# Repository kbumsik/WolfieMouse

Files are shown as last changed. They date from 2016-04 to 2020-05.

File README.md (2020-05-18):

# WolfieMouse

WolfieMouse is a robotics project to build [a micromouse](https://en.wikipedia.org/wiki/Micromouse). This project covers three parts:

* Robotics algorithm for maze solving (C++)
* low-level hardware driver software (C and ARM assembly)
* Tools to capture and plot robot's sensor data (Python)
* Embedded hardware design and PCB design (KiCad, an open-source alternative to Altium)

This robot won:
  * **The Special Mention Award in 2018 IEEE Region 1 Micromouse Robotics Competition**.
  * **The 3rd Place Award in 2019 IEEE Region 1 Micromouse Robotics Competition**.

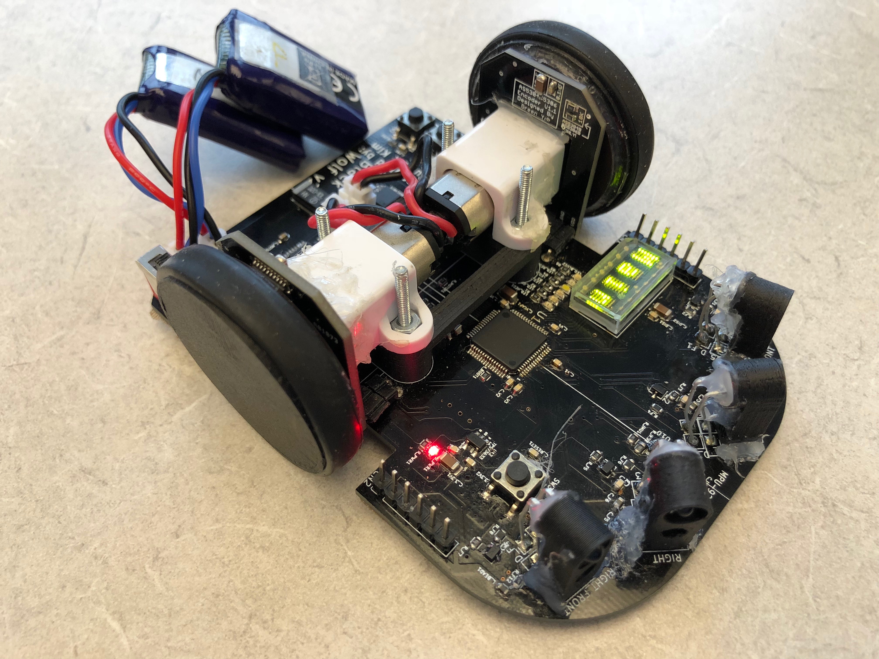
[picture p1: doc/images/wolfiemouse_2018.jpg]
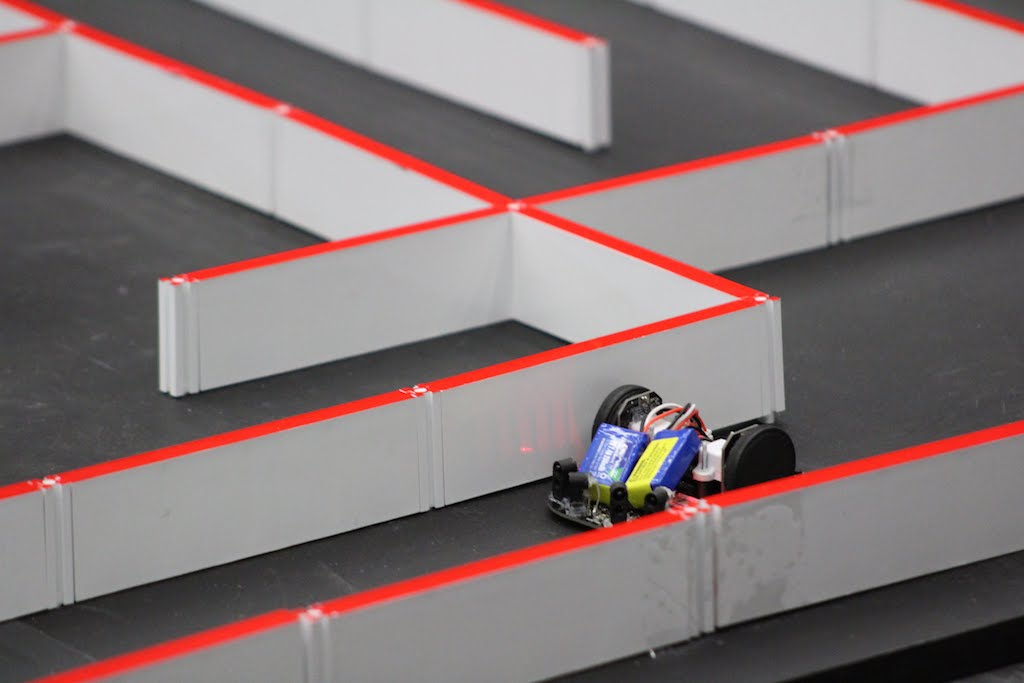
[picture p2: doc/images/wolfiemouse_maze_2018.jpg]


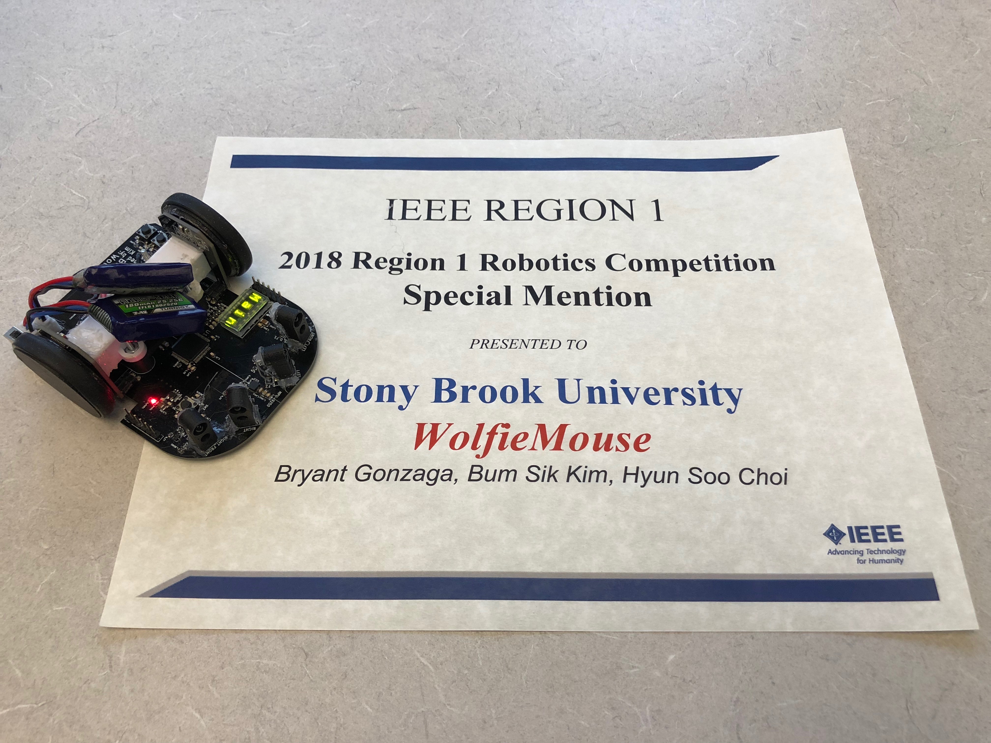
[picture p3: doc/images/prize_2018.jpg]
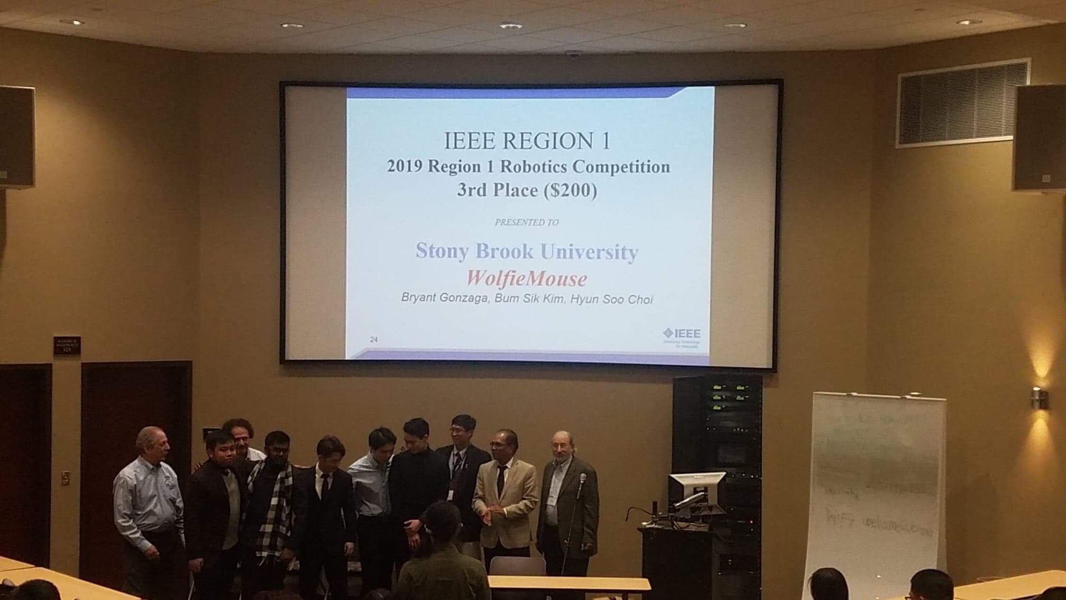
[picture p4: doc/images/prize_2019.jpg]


## Get started

If you don't know what is micromouse competition, [this document will help.](doc/What-is-Micromouse.md).

Requires tools:
* [GNU Arm Embedded Toolchain](https://developer.arm.com/open-source/gnu-toolchain/gnu-rm) and [Makefile](https://www.gnu.org/software/make/manual/make.html) to build program for the robot.
* [OpenOCD](http://openocd.org/) to upload the program to the robot and to debug.
* [KiCad](http://kicad-pcb.org/) to design a PCB hardware.

Otherwise, a [Vagrant](https://www.vagrantup.com/) virtual machine environment is provided to skip installing the above tools.

If you whish to start with this project, see [get stared document](doc/Get-started.md).

## Documentation

See [documentation section.](doc/)

## Directory descriptions

* `doc`: Documentation folder
* `firmware`: The robot's program folder, including robotics algorithms and hardware drivers
* `simulation`: Programs to test algorithms on a desktop computer
* `tools`: Contains robot sensor data capturing tools and scripts for Vagrant machine.

## Gallery

Terminal-based simulation program. `M` stands for the position of the robot, `D` stands for the position of the goal in the maze, and `S` stands for the starting position.

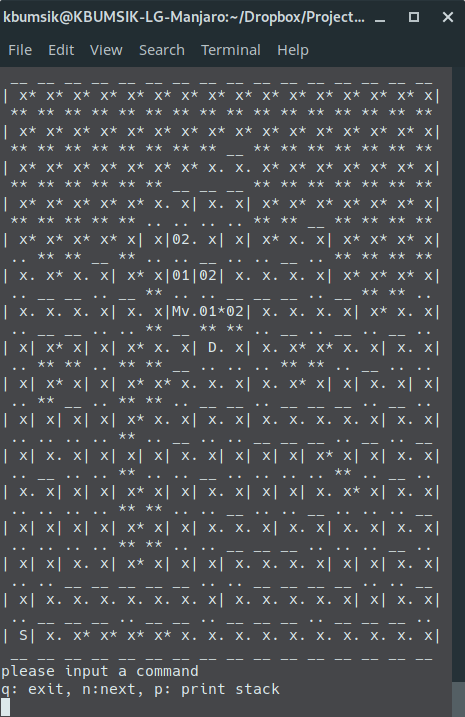
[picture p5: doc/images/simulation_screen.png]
simulation


Schematic overview.

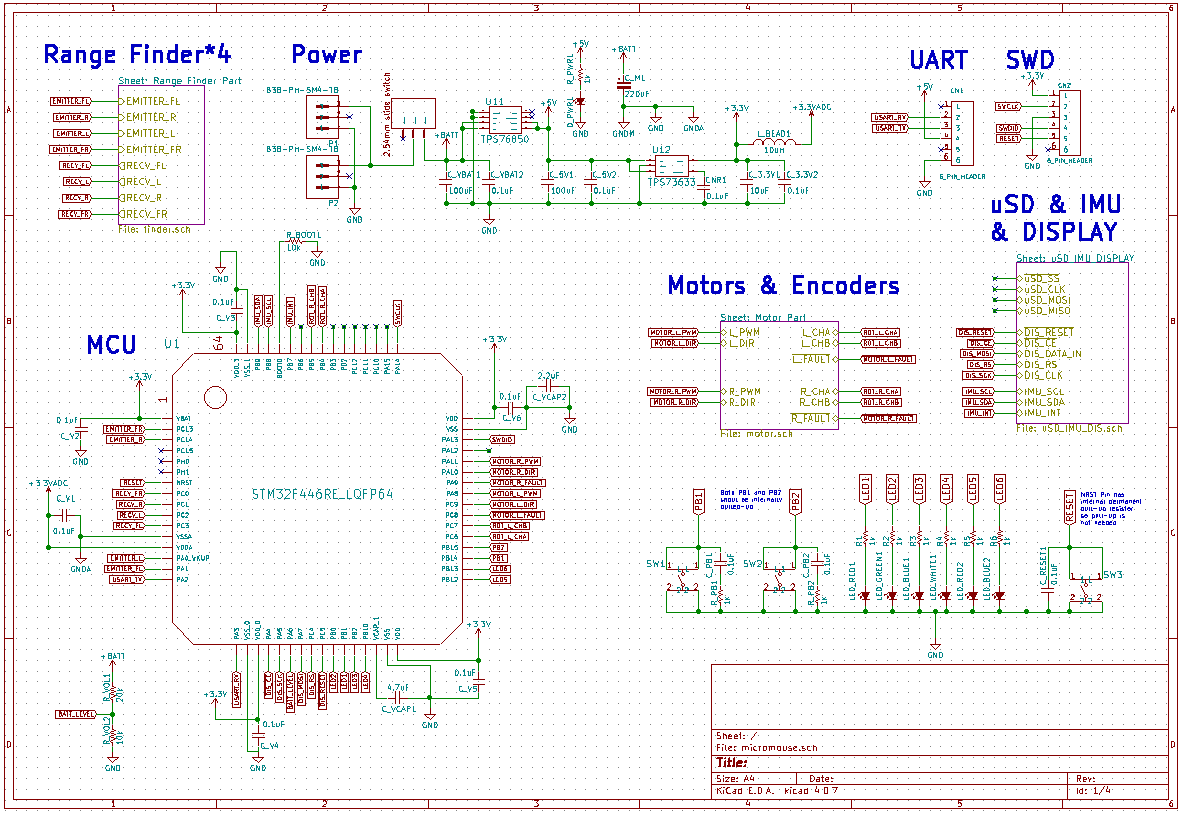
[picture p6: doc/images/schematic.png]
schematic_overview


PCB Footprint overview.

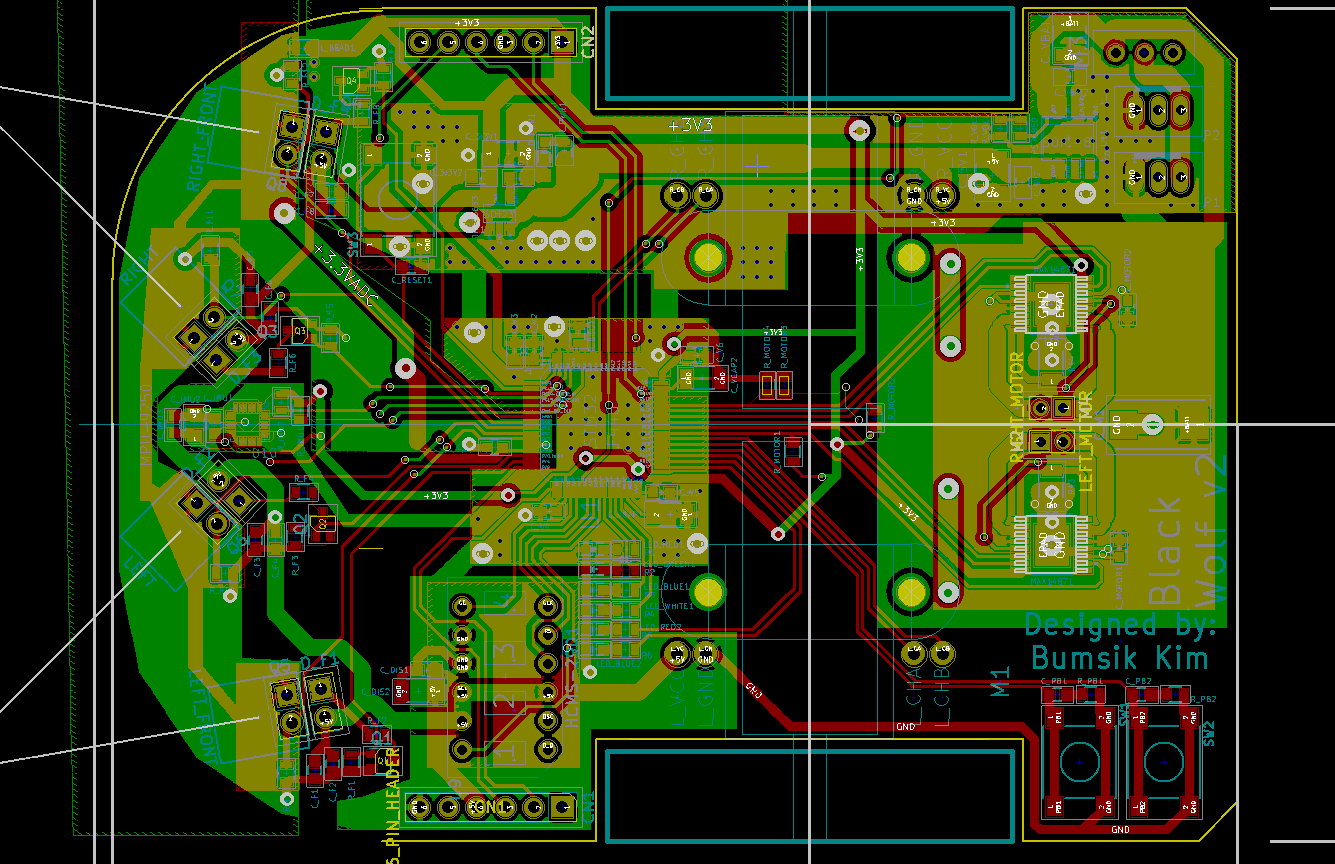
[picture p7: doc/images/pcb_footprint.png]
pcb_overview


## License and Credits

Source code in `firmware` and `simulation` folders are licensed under [GPLv2.1](https://www.gnu.org/licenses/old-licenses/lgpl-2.1.en.html).

External libraries (FreeRTOS, CMSIS, STM32F4 HAL) under `firmware/lib` follow their own terms.

The fundamental hardware design is inspired by [Project Futura](http://micromouseusa.com/?page_id=1342) by [Green Ye](http://www.greenye.net/).

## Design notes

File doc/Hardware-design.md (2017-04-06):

# Hardware Design

* Design reference: [Project Futura](http://micromouseusa.com/?page_id=1342)

## WolfieMouse v1.0

The basic ideas of our first mouse is following:

> Use as many digital components as possible, to eliminate design concerns on analog

To observe the ideas above, the micromouse features:

* STM32F446RET 32-bit ARM Cortex-M Microcontroller @180MHz
  * 512kB of Flash, 128kB of SRAM
  * One of the fastest microcontroller for 64-pin package
* VL6180X ToF Range sensor \*3 (or \*4)
  * Eliminates analog concern of Infrad LEDs/Phototransistors combo
  * Use PCA9546A I2C multiplexer to communicate between 4 indentical sensors
* MAX14871 full-bridge DC motor driver \*2
  * Avoids electrical and timing issues on H-bridge and MOFSET design
* Micro SD card reader
  * Easy to log and read data for designers, instead of use of SPI memory
* 4 Character LED display
* MPU9250 digital Inertial Measurement Unit (IMU)
* 5:1 Micro Metal Gearmotor HP by Polou *2
  * AS5304A magnetic encoder & AS5000-MR20-44 magnetic ring combo for rotary encoder of each motors

### Gallery of WolfieMouse 1.0

Schematic overview. See the whole schemetic [here (PDF).](hardware_design/schematic_2017_Feb.pdf) 

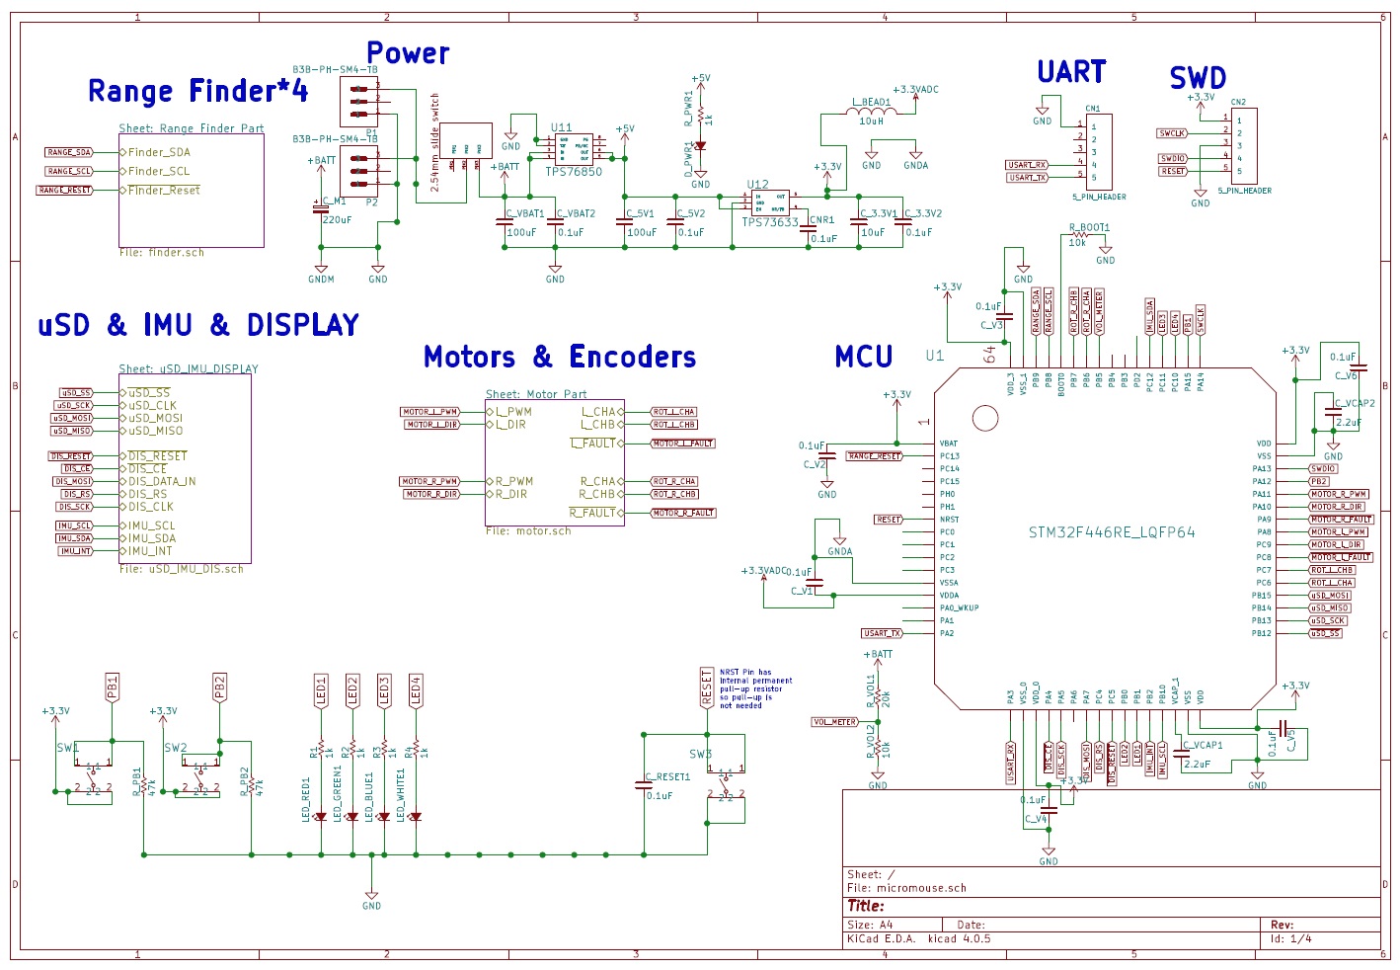
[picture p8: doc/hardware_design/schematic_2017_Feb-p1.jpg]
schematic_overview


PCB Footprint overview. Use [KiCad](http://kicad-pcb.org/) and open `hardware` dicrectory to see footprint.

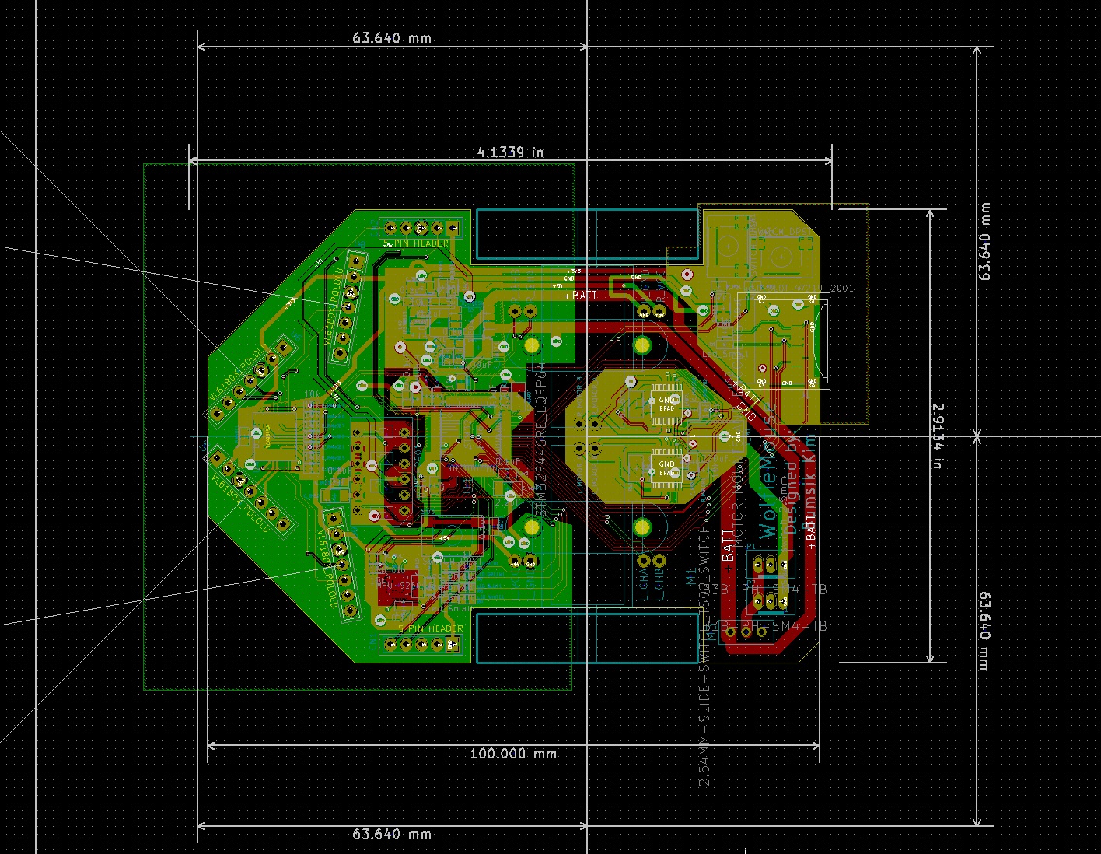
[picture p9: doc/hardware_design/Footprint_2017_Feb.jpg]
pcb_overview


## WolfieMouse v2.0

### What need to fixed from v1.0

1. The bed for motor is somewhat high - we need to make it lower.
2. Some part didn't work well due to bad soldering

### Design Goal

1. [Replace range sensor](#Range-sensor)
2. Add a buzzer
3. Add a bluetooth device
4. Try using back side of the board
5. Minor changes like changing position of chips

### Range sensor

* [A perfect description on designing range sensor](http://micromouseusa.com/wp-content/uploads/2014/02/lecture-5-Parts_design-choicespart1.pptx)

#### Parts candidate

* Emitter
  * SFH4550, 850nm: [Datasheet](http://www.osram-os.com/Graphics/XPic7/00209835_0.pdf)
  , [Digi-key](http://www.digikey.com/product-detail/en/osram-opto-semiconductors-inc/SFH-4550/475-1200-ND/806365)
  * SFH4555, 850nm: [Datasheet](http://www.osram-os.com/Graphics/XPic6/00209799_0.pdf)
  , [Digi-key](http://www.digikey.com/product-detail/en/osram-opto-semiconductors-inc/SFH-4555/475-3023-ND/2205957)
  * SFH4545, 925nm: [Datasheet](http://www.osram-os.com/Graphics/XPic4/00209805_0.pdf),
  [Digi-key](http://www.digikey.com/product-detail/en/osram-opto-semiconductors-inc/SFH-4545/475-2919-ND/2205955)
* Phototransistor
  * BPW85B, 850nm: [Datasheet](http://www.vishay.com/docs/81531/bpw85a.pdf)
  [Digi-key](http://www.digikey.com/product-detail/en/vishay-semiconductor-opto-division/BPW85B/BPW85B-ND/4071265)
  * TEFT4300, 925nm: [Datasheet](http://www.vishay.com/docs/81549/teft4300.pdf)
  [Digi-key](http://www.digikey.com/product-detail/en/vishay-semiconductor-opto-division/TEFT4300/751-1041-ND/1681175)

### Buzzer

### Bluetooth

### Minor Changes

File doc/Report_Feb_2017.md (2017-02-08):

# WolfieMouse Report Feb, 2017

## How Was 2016 Micromouse Competition

We had [a competiton in 2016](https://meetings.vtools.ieee.org/m/37907). Although
we had some achievements, such as making the actual mouse hardware, it was a big fail!
The mouse didn't work in the maze. The main reason was because we spent too much time
doing trial and error with hardware and couldn't finish driver software parts.

### What we achived

* We completed a PCB design and soldering for a mouse hardware.
* We made a basic algorithm and simulation that actually works.

### What problem we had

* The main problem: We didn't finished making software driver in time.
* Soldering problem: some part of hardware (display, SD card) didn't work 
due to bad soldering.
* Algorithm: we need to make algorithm better to reduce solving time (e.g. diagnal movement)

## What I did after competiton

I had made some improvement last semester. It was mostly for making project more
approachable.

* Improved driver software. Now the mouse should start working.
* Improved programming environment so that newcommers don't need to struggle 
setting up.

## What we need to do for 2017 competion

The next micromouse competition is around the middle of April. Even though
we already have a working mouse, we are planing to make another mouse with
improved design.

* Attach simulation part with an actual mouse.
* Improve hardware design. There are many things to fix our PCB board.
* Adopt better alorithm.
* Actual test on the maze in our lab.

## WolfieMouse need help!

This project has been done by one person. However, this project _cannot_ be done by
one person. I need your help. If you participate you can learn the following but
not limited to:

* Algorithm design
* Embedded system software development (C/C++)
* Hardware redesign, PCB design, and surface-mount device soldering. 
* 3D printing.
* Collaboration tools such as Git.

## Expected timeline and workload

Micromouse is a big project. There is a lot of work needed to be done in order to finish in two
months. I will usually have two meetings per week but we may have more, if needed.

* Feb - 1st week of March: Get to know about theory. Redesign hardware.
* 2nd week, March: Build a new Micromouse.
* 3rd week, March - to the date of competition(April): Test the mouse and improve software.

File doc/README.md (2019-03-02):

# Documentation

## Table of Contents

* Tutorial
  * [What is micromouse competition?](#What-is-Micromouse)
  * [Get-Started](#Getting-Started)
  * [Vagrant-HOWTO](#Vagrant-HOWTO)
  * [Github-HOWTO](#Github-HOWTO)
  * [KiCad-HOWTO](#KiCad-HOWTO)

* Code Documentation
  * [Class Design](Class-design.md)
  * [Hardware Design](Hardware-design.md)

* Reports
  * [Feb 2017 report](Report_Feb_2017.md)

## What is Micromouse

* [2015 Micromouse IEEE Region 1 competition slide](http://ewh.ieee.org/reg/1/sac/assets/Documents/2015-R1-Micromouse-Competition.pdf)
* [Micromouse Rule](http://ewh.ieee.org/reg/1/sac/assets/Documents/2016/2016-R1-Micromouse-Guideline.pdf)

### Video

* [Simeple example video](https://www.youtube.com/watch?v=_L9rkLAskWU)
* [Crazay World record video](https://youtu.be/blpnbIzq6G0?t=30s)

## Getting Started

### Quick setup using a virtual machine (recommended)

1. Install tools
    * [git](https://git-scm.com/downloads)
    * [VirtualBox](https://www.virtualbox.org/wiki/Downloads)
    * [VirtualBox Extension Pack](https://www.virtualbox.org/wiki/Downloads). [(Video)](https://youtu.be/P5exlXPF1SM)
    * [Vagrant](https://www.vagrantup.com/)
    * [MobaXterm](http://mobaxterm.mobatek.net/) for windows, [XQuartz](https://www.xquartz.org/) for macOS
    * Add to `PATH` with following folders: [(Video)](https://youtu.be/biMVFUH0grA).
        * git: `{your-git-installation-path}/Git/bin` and `{your-git-installation-path}/Git/usr/bin`
        * VirtualBox: `{your-VirtualBox-installation-path}/Oracle/VirtualBox`
2. [Fork this repo and clone it](HOWTO/Github_HOWTO.md#Set-up-your-repository)
3. Run `$ vagrant up` to install VM. [(Video)](https://youtu.be/IwcibyR7uL4)
    * This is a virtual machine installation command. Requires around 8GB.
    * This will take at least 20 minutes. Have a cup of coffee :)
4. After successful install, connect to the machine via SSH using MobaXterm. [(Video)](https://youtu.be/jf9KIUKjGEk)
5. `$ cd ~/wolfiemouse`. This is our project root directory.

### Regular setup without virtual machine (when virtual machine not working properly)

To be added.

## Vagrant-HOWTO

Vagrant is a tool for Virtual Machine. Vagrant abstract virtual machine interfaces
and will automate system configuration of a VM, so we will have a unified 
working environment.

### Prerequisites

See `Install tools` section in [Get Started Document](../Get-started.md). Don't
forget to add `Git` directories in `PATH`.

### How to boot a vagrant VM

The following command will boot up the VM in background:

> $ vagrant up

If you run the above code for the first time, it will install the operating
system and the software we use in the project. This initial process will take
around 20 minuetes so have a cup of coffee.

### How to connect a terminal(SSH) to the VM

We can connect the virtual machine through SSH(remote terminal). The defualt
configuration to connect is:

* Address: 127.0.0.1
* Port: 2222
* User: vagrant

### How to close the VM

Simple, just commend:

> $ vagrant halt

### How to delete the VM

This is also simple. Run:

> $ vagrant destroy

You can re-install the VM using `$ vagrant up` any time.

### Troubleshooting

1. It says we need to install `SSH`: Don't forget add `Git` directories
(`{your-git-installation-path}/Git/bin` and `{your-git-installation-path}/Git/usr/bin`)
in `PATH` environment variable. Git has SSH tools for you.
2. Timeout error : Firstly, check if your CPU supports virtualization (VT-x).
If it doesn't you cannot use the VM and Vagrant. Consider installing Ubuntu in
a separated partition. If your CPU supports VT-x but you still have that problem,
the BIOS might disabled the CPU virtualization feature. Go to BIOS and enable it.

## Github-HOWTO

Reference: https://help.github.com/articles/syncing-a-fork/

### Set up your repository

* Fork our github repo https://github.com/kbumsik/WolfieMouse
* Clone your forked repo. e.g:

> $ git clone --recursive https://github.com/{your-id}/WolfieMouse

* Add our repo as a new remote `upstream`

> $ git remote add upstream https://github.com/kbumsik/WolfieMouse

### Make new change input your repository

Check what you changed

> $ git status

Add your changes into staged mode

> $ git add {files-you-changed} or  $ git add --all

Double check change

> $ git status

Commit change

> $ git commit -m "some message. e.g. what you changed"

Push it to your repository

> $ git push origin master

Then you can make a pull request later

### Update your repo with `upstream`

* Update your local repo with `upstream`

First get information of `upstream`

> $ git fetch upstream

next,

> $ git pull upstream master

or

> $ git rebase upstream/master

Then

> $ git submodule update --recursive

* push it to `origin` repo, your forked repository

> $ git push origin master

### Useful git commands

* `git log --decorate --all --graph`
* `git fetch upstream master`
* `git stash` and `git stash pop`
* `git diff <commit>`

## KiCad-HOWTO

KiCad is one of the most famous EDA (Electronic Design Automation) software.
This is mainly developed and supported my CERN. It provides a full set of
PCB design tools, including shcematic, PCB footprint, and 3D model generation.
The best thing about KiCad is absolutly free.

However, it comes at a price. I mean it is not easy to get used to it.
Especially, there are a lot of _very_ tricky thing you would hardly figure out 
(seriously.) So I highly recommend going there some tutorials. By the way, do
not try to read manuals. It is not worth time :P

### Recommended Video Tutorials

* [(Reletivly) quick tutorial from scrach to making an actual device](https://contextualelectronics.com/learning/getting-to-blinky-4-0/)
* [Detail Youtube series](https://www.youtube.com/user/contextualelectronic/playlists)

### Other Tutorials

* [List of tutorials from KiCad official website](http://kicad-pcb.org/help/tutorials/)

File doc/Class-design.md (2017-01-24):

# Maze solving part

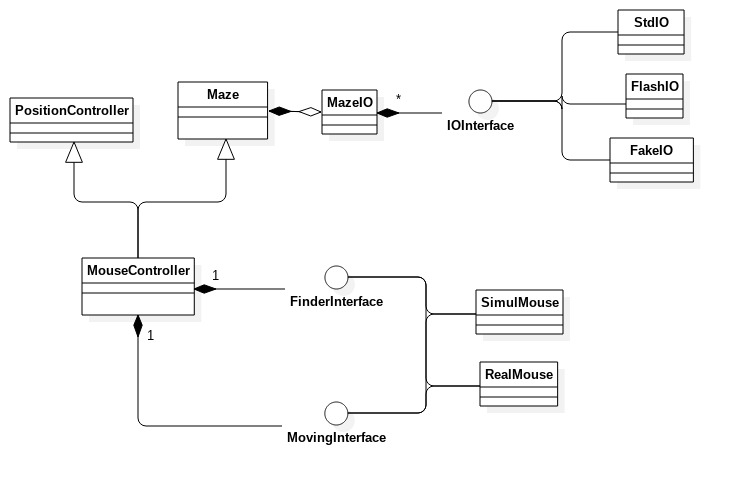
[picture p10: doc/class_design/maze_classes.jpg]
maze classes diagram


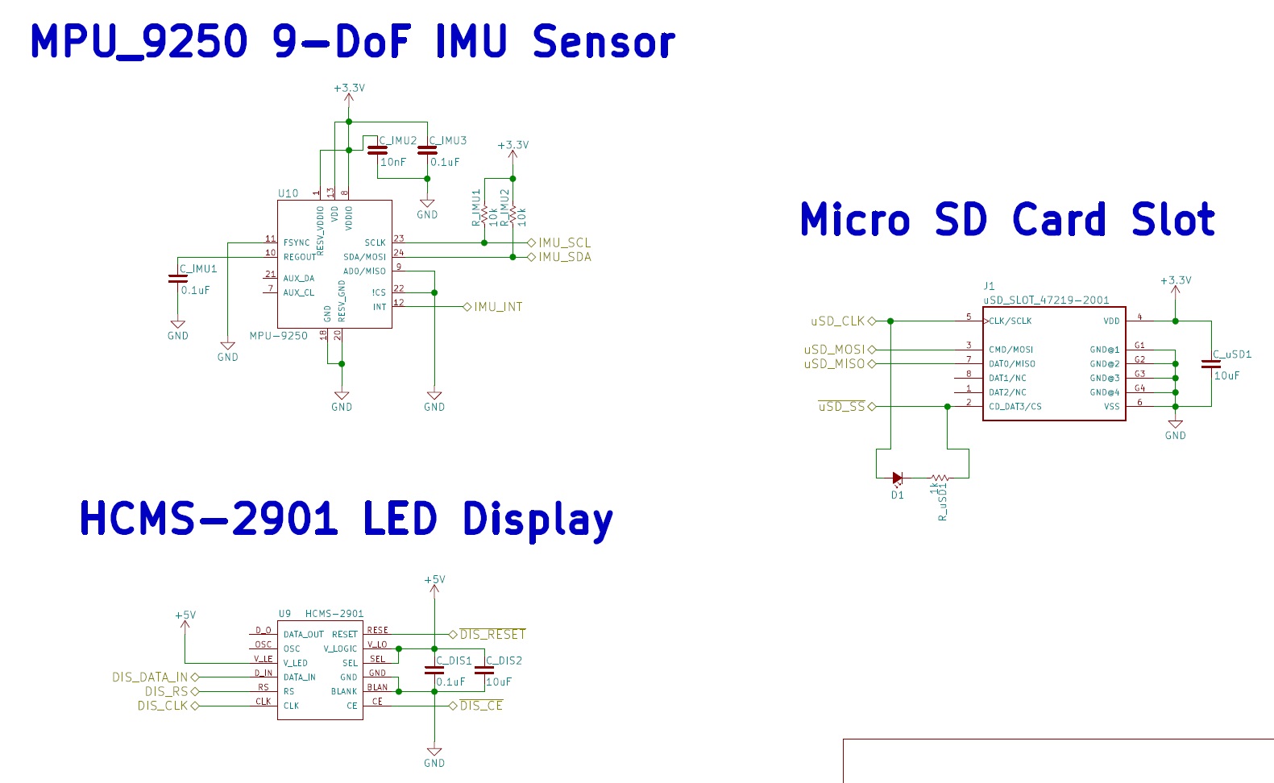
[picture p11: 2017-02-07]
doc/hardware_design/schematic_2017_Feb-p4.jpg

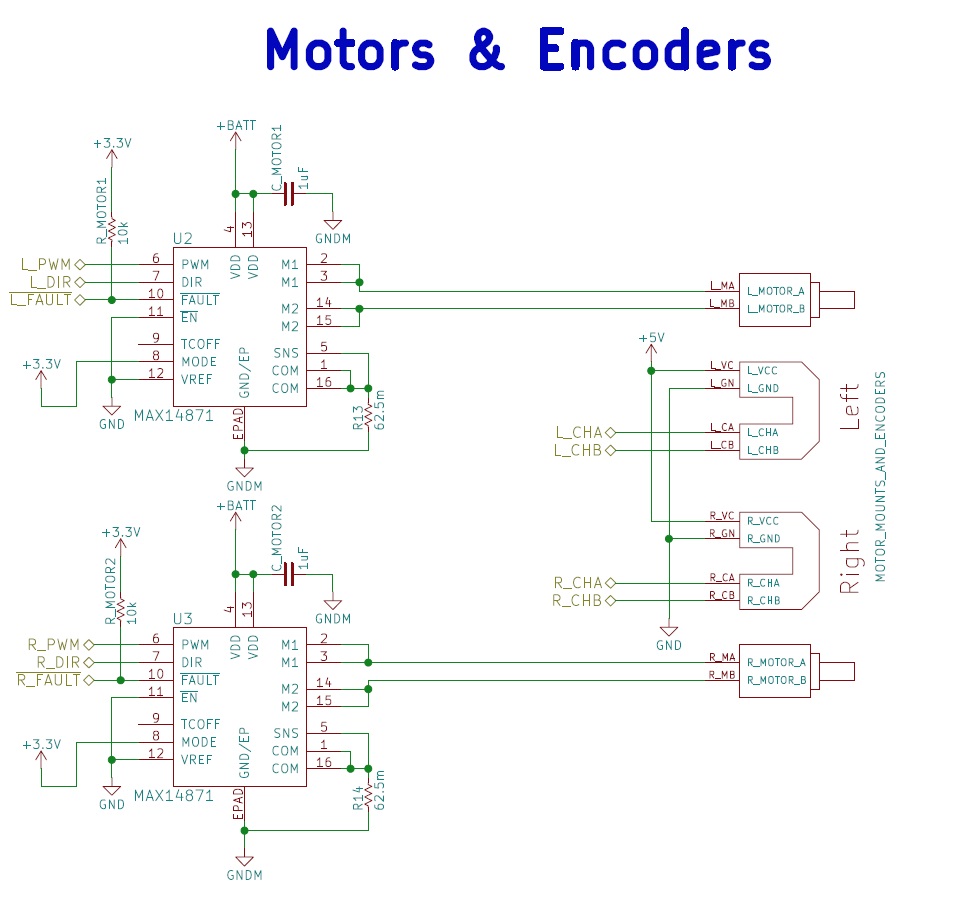
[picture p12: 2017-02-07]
doc/hardware_design/schematic_2017_Feb-p2.jpg

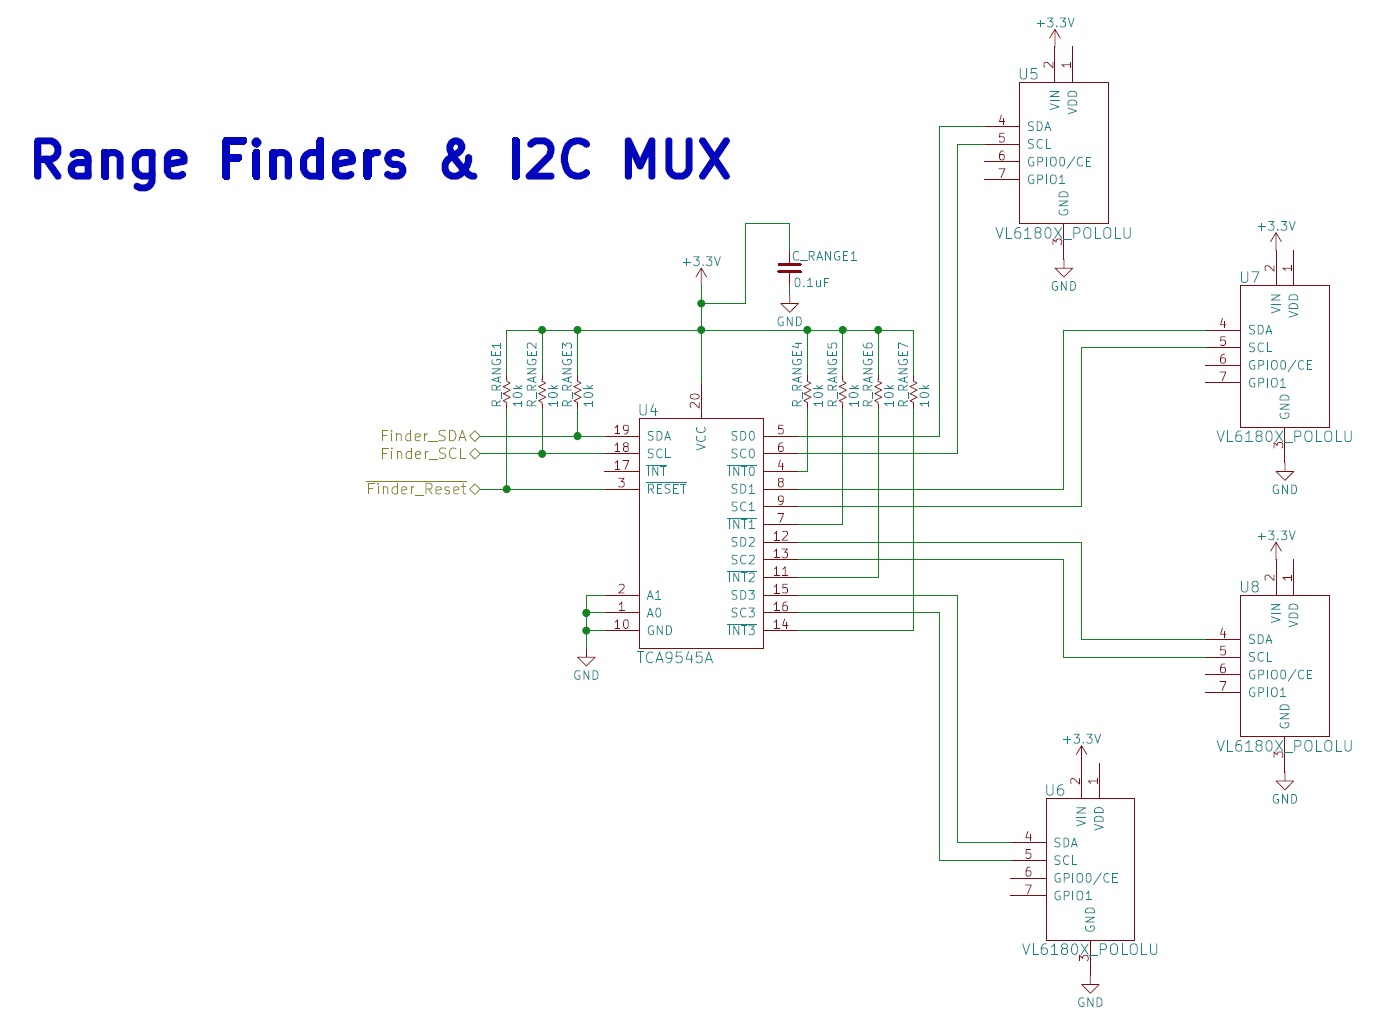
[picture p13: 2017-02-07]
doc/hardware_design/schematic_2017_Feb-p3.jpg

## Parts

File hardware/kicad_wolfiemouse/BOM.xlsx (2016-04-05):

 | Reference | # | Value | Manufacturer | Manufacturer # | Digi-key part # | Discription | Cost | ext. Cost | Footprint | Datasheet
1 | U1 | 1 | STM32F446RE_LQFP64 | STMicroelectronics | STM32F446RET6 | 497-15376-ND |  | 9.71 | 9.71 | footprints_micromouse:STM32F446_LQFP64
2 | LED_RED1, D_PWR1 | 2 | Led_Small | Vishay Semiconductor Opto Division | VLMS1300-GS08 | VLMS1300-GS08CT-ND |  | 0.43 | 0.86 | LEDs:LED_0603
3 | LED_GREEN1 | 1 | Led_Small | Vishay Semiconductor Opto Division | VLMTG1300-GS08 | VLMTG1300-GS08CT-ND |  | 0.43 | 0.43 | LEDs:LED_0603
4 | LED_BLUE1, D1 | 2 | Led_Small | Vishay Semiconductor Opto Division | VLMB1300-GS08 | VLMB1300-GS08CT-ND |  | 0.43 | 0.86 | LEDs:LED_0603
5 | LED_WHITE1 | 1 | Led_Small | Vishay Semiconductor Opto Division | VLMW1300-GS08 | VLMW1300-GS08CT-ND |  | 0.43 | 0.43 | LEDs:LED_0603
6 | C_IMU2 | 1 | 10nF | Yageo | CC0805KRX7R9BB103 | 311-1136-1-ND | CAP CER 10000PF 50V X7R 0805 | 0.1 | 0.1 | Capacitors_SMD:C_0805
7 | C_VBAT2, C_5V2, CNR1, C_3.3V2, C_RESET1, C_V1, C_V2, C_V3, C_V4, C_V5, C_V6, C_RANGE1, C_DIS1, C_IMU1, C_IMU3 | 15 | 0.1uF | Vishay Vitramon | VJ0603Y104KXXAC | 720-1378-1-ND | CAP CER 0.1UF 25V X7R 0603 | 0.34 | 5.1 | Capacitors_SMD:C_0603
8 | C_MOTOR1, C_MOTOR2 | 2 | 1uF | Yageo | CC0603KRX5R8BB105 | 311-1445-1-ND | CAP CER 1UF 25V X5R 0603 | 0.1 | 0.2 | Capacitors_SMD:C_0603
9 | C_VCAP1, C_VCAP2 | 2 | 2.2uF | Yageo | CC1206KKX7R7BB225 | 311-1957-1-ND | CAP CER 2.2UF 16V X7R 1206 | 0.21 | 0.42 | Capacitors_SMD:C_1206
10 | C_3.3V1, C_DIS2, C_uSD1 | 3 | 10uF | Yageo | CC1206ZKY5V7BB106 | 311-1376-1-ND | CAP CER 10UF 16V Y5V 1206 | 0.22 | 0.66 | Capacitors_SMD:C_1206
11 | C_VBAT1, C_5V1 | 2 | 100uF | Yageo | CC1210MKX5R7BB107 | 311-2052-1-ND | CAP CER 100UF 16V X5R 1210 | 1.92 | 3.84 | Capacitors_SMD:C_1210
12 | C_M1 | 1 | 220uF | Vishay Sprague | TR3D227K010C0150 | 718-1777-1-ND | CAP TANT 220UF 10V 10% 2917 | 1.31 | 1.31 | Capacitors_Tantalum_SMD:TantalC_SizeD_EIA-7343_HandSoldering
13 | R13, R14 | 2 | 62.5m | Vishay Dale | WSL1206R0600FEA | WSLC-.06CT-ND | RES SMD 0.06 OHM 1% 1/4W 1206 | 0.92 | 1.84 | Resistors_SMD:R_0603
14 | R1, R2, R3, R4, R_PWR1, R_uSD1 | 6 | 1k | Vishay Dale | CRCW06031K00FKEA | 541-1.00KHCT-ND | RES SMD 1K OHM 1% 1/10W 0603 | 0.081 | 0.486 | Resistors_SMD:R_0603
15 | R_BOOT1, R_VOL2, R_MOTOR1, R_MOTOR2, R_RANGE1, R_RANGE2, R_RANGE3, R_RANGE4, R_RANGE5, R_RANGE6, R_RANGE7, R_IMU1, R_IMU2 | 13 | 10k | Vishay Dale | CRCW060310K0FKEA | 541-10.0KHCT-ND | RES SMD 10K OHM 1% 1/10W 0603 | 0.081 | 1.053 | Resistors_SMD:R_0603
16 | R_VOL1 | 1 | 20k | Vishay Dale | CRCW060320K0JNEA | 541-20KGCT-ND | RES SMD 20K OHM 5% 1/10W 0603 | 0.1 | 0.1 | Resistors_SMD:R_0603
17 | R_PB2, R_PB1 | 2 | 47k | Vishay Dale | CRCW060347K0JNEA | 541-47KGCT-ND | RES SMD 47K OHM 5% 1/10W 0603 | 0.1 | 0.2 | Resistors_SMD:R_0603
18 | L_BEAD1 | 1 | 10uH | Murata Electronics North America | BLM18KG601SN1D | 490-5258-1-ND | FERRITE BEAD 600 OHM 0603 1LN | 0.1 | 0.1 | Resistors_SMD:R_0603
19 | M3 | 1 | 2.54MM-SLIDE-SWITCH_TS02_SWITCH |  |  |  |  |  | 0 | pcb1:2.54MM-SLIDE-SWITCH_TS02_SWITCH
20 | U11 | 1 | TPS76850 | Texas Instruments | TPS76850QD | 296-2751-5-ND | IC REG LDO 5V 1A 8SOIC | 2.98 | 2.98 | footprints_micromouse:TPS76850_SOIC-8
21 | U12 | 1 | TPS73633 | Texas Instruments | TPS73633DBVR | 296-27064-1-ND | IC REG LDO 3.3V 0.4A SOT23-5 | 2.05 | 2.05 | footprints_micromouse:TPS73633_SOT-23
22 | SW1, SW2, SW3 | 3 | SWITCH_DPST | C&K Components | PTS645SL50SMTR92 LFS | CKN9088CT-ND | SWITCH TACTILE SPST-NO 0.05A 12V | 0.29 | 0.87 | Buttons_Switches_SMD:SW_SPST_PTS645
23 | CN1, CN2 | 2 | 5_PIN_HEADER |  |  |  |  |  | 0 | Pin_Headers:Pin_Header_Straight_1x05
24 | P1, P2 | 2 | B3B-PH-SM4-TB | JST Sales America Inc. | B3B-PH-K-S(LF)(SN) | 455-1705-ND | CONN HEADER PH TOP 3POS 2MM | 0.19 | 0.38 | footprints_micromouse:JST_B3B-PH_HEADER
25 | U2, U3 | 2 | MAX14871 | Maxim Integrated | MAX14871EUE+T | MAX14871EUE+CT-ND | IC MOTOR DVR DC FULL BR 16TSSOP | 4.03 | 8.06 | footprints_micromouse:TSSOP-16_EP
26 | M1 | 1 | MOTOR_MOUNTS_AND_ENCODERS |  |  |  |  |  | 0 | footprints_micromouse:FUTURA-1.0-MOTOR-MOUNT-TEMPLATE
27 | U5, U6, U7, U8 | 4 | VL6180X_POLOLU |  |  |  |  |  | 0 | footprints_micromouse:VL6180X_POLOLU_Pin_Header_Straight_1x07
28 | U4 | 1 | TCA9545A | Texas Instruments | TCA9545APWR | 296-40577-1-ND | IC I2C SW 4CH W/RESET 20TSSOP |  | 0 | Housings_SSOP:TSSOP-20_4.4x6.5mm_Pitch0.65mm
29 | U9 | 1 | HCMS-2901 | Avago (Broadcom company) | HCMS-2901 | 516-2964-ND | LED DISPLAY 5X7 4CHAR 3.8MM YLW | 22.92 | 22.92 | footprints_micromouse:HCMS-2903
30 | U10 | 1 | MPU-9250 | InvenSense | MPU-9250 | 1428-1019-1-ND | GYRO/ACCEL/COMPASS/9-AXIS | 10.64 | 10.64 | footprints_micromouse:MPU-9250
31 | J1 | 1 | uSD_SLOT_47219-2001 | Molex, LLC | 5009010801 | WM19081CT-ND | CONN MICRO SD CARD HINGED TYPE |  | 0 | footprints_micromouse:uSD_MOLEX_47219-2001
 |  |  |  |  |  |  |  |  | 75.599

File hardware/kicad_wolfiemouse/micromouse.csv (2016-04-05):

Reference | Value | Footprint | Datasheet
U1 | STM32F446RE_LQFP64 | footprints_micromouse:STM32F446_LQFP64
LED_BLUE1 | Led_Small | LEDs:LED_0603
LED_WHITE1 | Led_Small | LEDs:LED_0603
R3 | 1k | Resistors_SMD:R_0603
R4 | 1k | Resistors_SMD:R_0603
M3 | 2.54MM-SLIDE-SWITCH_TS02_SWITCH | pcb1:2.54MM-SLIDE-SWITCH_TS02_SWITCH
U11 | TPS76850 | footprints_micromouse:TPS76850_SOIC-8
U12 | TPS73633 | footprints_micromouse:TPS73633_SOT-23
C_VBAT1 | 100uF | Capacitors_SMD:C_1210
C_VBAT2 | 0.1uF | Capacitors_SMD:C_0603
C_5V2 | 0.1uF | Capacitors_SMD:C_0603
C_5V1 | 100uF | Capacitors_SMD:C_1210
CNR1 | 0.1uF | Capacitors_SMD:C_0603
C_3.3V1 | 10uF | Capacitors_SMD:C_1206
C_3.3V2 | 0.1uF | Capacitors_SMD:C_0603
R_PWR1 | 1k | Resistors_SMD:R_0603
D_PWR1 | Led_Small | LEDs:LED_0603
R_PB2 | 47k | Resistors_SMD:R_0603
SW2 | SWITCH_DPST | Buttons_Switches_SMD:SW_SPST_PTS645
SW3 | SWITCH_DPST | Buttons_Switches_SMD:SW_SPST_PTS645
C_RESET1 | 0.1uF | Capacitors_SMD:C_0603
R_PB1 | 47k | Resistors_SMD:R_0603
SW1 | SWITCH_DPST | Buttons_Switches_SMD:SW_SPST_PTS645
R_BOOT1 | 10k | Resistors_SMD:R_0603
C_VCAP1 | 2.2uF | Capacitors_SMD:C_1206
C_V5 | 0.1uF | Capacitors_SMD:C_0603
C_VCAP2 | 2.2uF | Capacitors_SMD:C_1206
C_V6 | 0.1uF | Capacitors_SMD:C_0603
C_V3 | 0.1uF | Capacitors_SMD:C_0603
C_V2 | 0.1uF | Capacitors_SMD:C_0603
C_V1 | 0.1uF | Capacitors_SMD:C_0603
L_BEAD1 | 10uH | Resistors_SMD:R_0603
R_VOL1 | 20k | Resistors_SMD:R_0603
R_VOL2 | 10k | Resistors_SMD:R_0603
C_V4 | 0.1uF | Capacitors_SMD:C_0603
C_M1 | 220uF | Capacitors_Tantalum_SMD:TantalC_SizeD_EIA-7343_HandSoldering
CN2 | 5_PIN_HEADER | Pin_Headers:Pin_Header_Straight_1x05
CN1 | 5_PIN_HEADER | Pin_Headers:Pin_Header_Straight_1x05
LED_GREEN1 | Led_Small | LEDs:LED_0603
R2 | 1k | Resistors_SMD:R_0603
LED_RED1 | Led_Small | LEDs:LED_0603
R1 | 1k | Resistors_SMD:R_0603
P2 | B3B-PH-SM4-TB | footprints_micromouse:JST_B3B-PH_HEADER
P1 | B3B-PH-SM4-TB | footprints_micromouse:JST_B3B-PH_HEADER
U2 | MAX14871 | footprints_micromouse:TSSOP-16_EP
U3 | MAX14871 | footprints_micromouse:TSSOP-16_EP
M1 | MOTOR_MOUNTS_AND_ENCODERS | footprints_micromouse:FUTURA-1.0-MOTOR-MOUNT-TEMPLATE
C_MOTOR1 | 1uF | Capacitors_SMD:C_0603
C_MOTOR2 | 1uF | Capacitors_SMD:C_0603
R_MOTOR1 | 10k | Resistors_SMD:R_0603
R_MOTOR2 | 10k | Resistors_SMD:R_0603
R13 | 62.5m | Resistors_SMD:R_0603
R14 | 62.5m | Resistors_SMD:R_0603
U5 | VL6180X_POLOLU | footprints_micromouse:VL6180X_POLOLU_Pin_Header_Straight_1x07
U7 | VL6180X_POLOLU | footprints_micromouse:VL6180X_POLOLU_Pin_Header_Straight_1x07
U8 | VL6180X_POLOLU | footprints_micromouse:VL6180X_POLOLU_Pin_Header_Straight_1x07
U6 | VL6180X_POLOLU | footprints_micromouse:VL6180X_POLOLU_Pin_Header_Straight_1x07
U4 | TCA9545A | Housings_SSOP:TSSOP-20_4.4x6.5mm_Pitch0.65mm
R_RANGE4 | 10k | Resistors_SMD:R_0603
R_RANGE5 | 10k | Resistors_SMD:R_0603
R_RANGE6 | 10k | Resistors_SMD:R_0603
R_RANGE7 | 10k | Resistors_SMD:R_0603
R_RANGE3 | 10k | Resistors_SMD:R_0603
R_RANGE2 | 10k | Resistors_SMD:R_0603
R_RANGE1 | 10k | Resistors_SMD:R_0603
C_RANGE1 | 0.1uF | Capacitors_SMD:C_0603
U9 | HCMS-2901 | footprints_micromouse:HCMS-2903
U10 | MPU-9250 | footprints_micromouse:MPU-9250
J1 | uSD_SLOT_47219-2001 | footprints_micromouse:uSD_MOLEX_47219-2001
C_DIS1 | 0.1uF | Capacitors_SMD:C_0603
C_DIS2 | 10uF | Capacitors_SMD:C_1206
D1 | Led_Small | LEDs:LED_0603
R_uSD1 | 1k | Resistors_SMD:R_0603
C_IMU1 | 0.1uF | Capacitors_SMD:C_0603
C_IMU3 | 0.1uF | Capacitors_SMD:C_0603
C_IMU2 | 10nF | Capacitors_SMD:C_0805
R_IMU2 | 10k | Resistors_SMD:R_0603
R_IMU1 | 10k | Resistors_SMD:R_0603
C_uSD1 | 10uF | Capacitors_SMD:C_1206

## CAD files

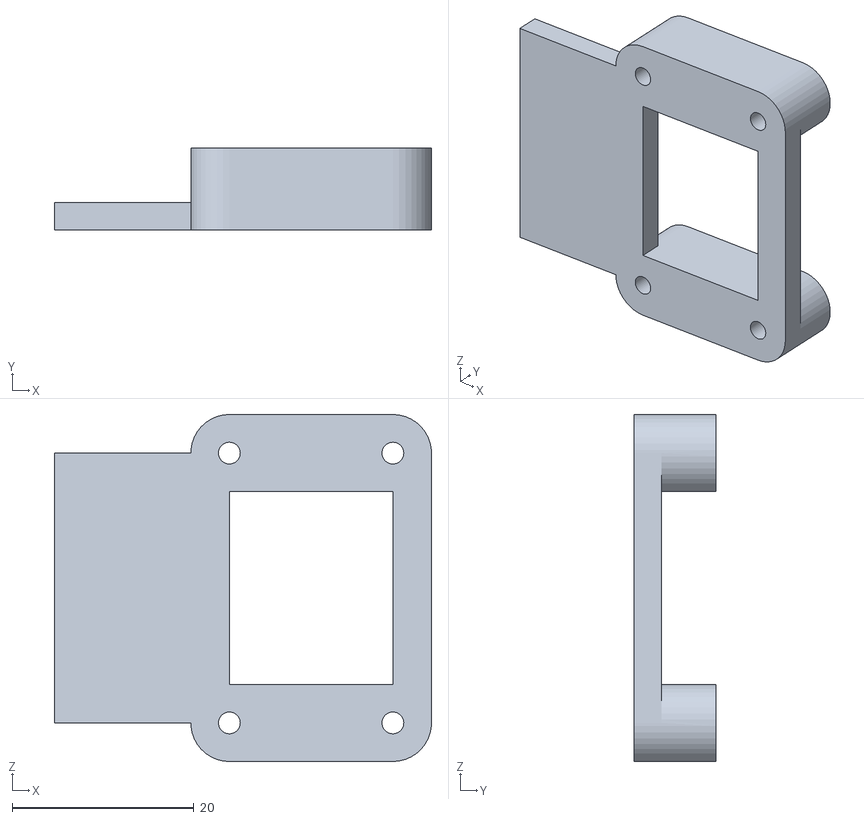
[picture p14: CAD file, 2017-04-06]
hardware/kicad_wolfiemouse/3D_Model/motor seat.STL
41.5 x 9.00 x 38.2

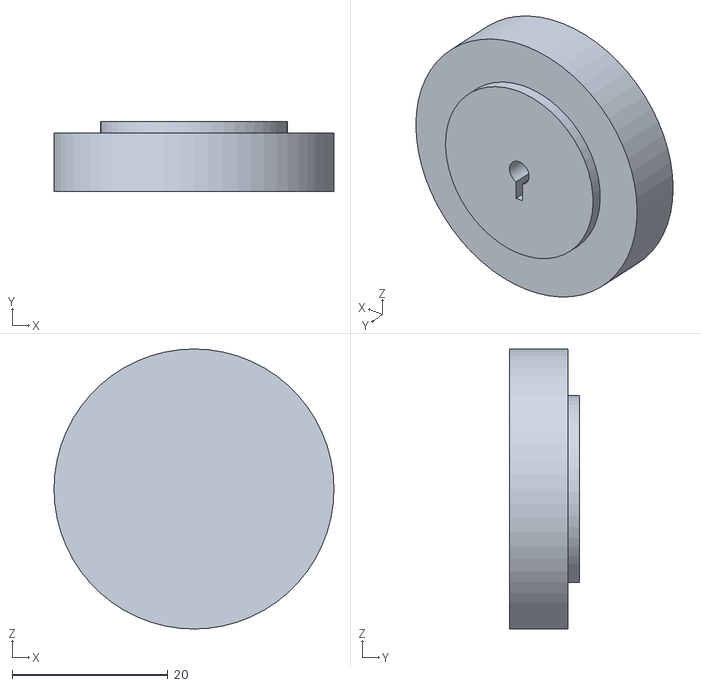
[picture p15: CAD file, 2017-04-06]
hardware/kicad_wolfiemouse/3D_Model/wheel.STL
36.0 x 9.00 x 36.0

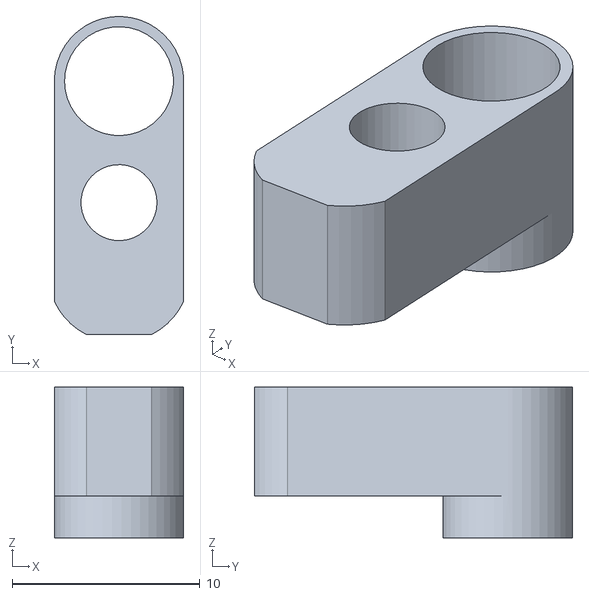
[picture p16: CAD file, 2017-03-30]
hardware/kicad_wolfiemouse/3D_Model/Sensor_Housing.STL
6.89 x 16.9 x 8.03

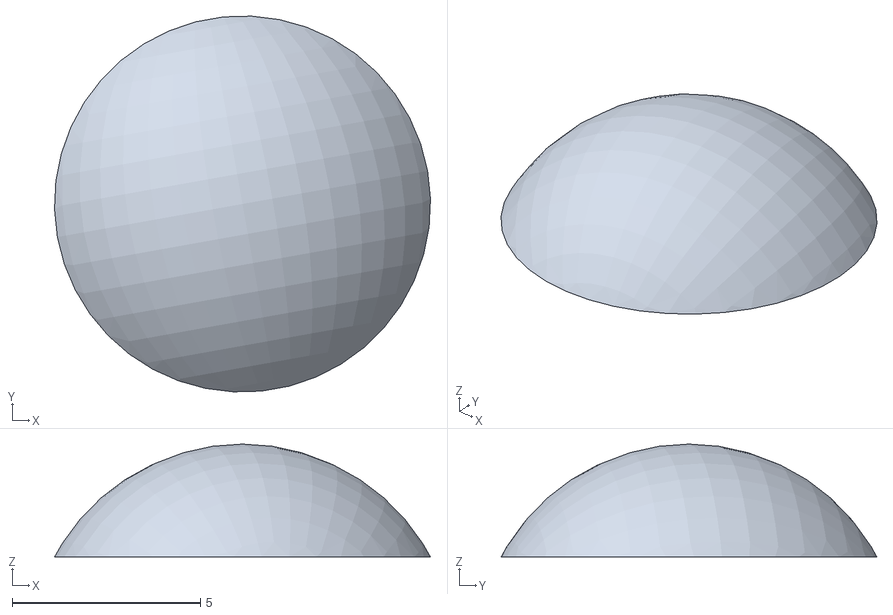
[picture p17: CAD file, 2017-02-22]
hardware/kicad_wolfiemouse/3D_Model/skate.stl
10.00 x 9.99 x 3.00

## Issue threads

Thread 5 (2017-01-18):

Adding the new hardware driver.

kbumsik, 2017-01-18:
I already wrote the hardware driver. We only need to integrate it.

- [x] : Add a simple blinky project
- [ ] : Make test prjects for each hardware component.
- [ ] : Add PID-controlled motor driver.
- [ ] : implement `finderInterface` and `moverInterface` integrating hardware driver.

kbumsik, 2017-03-18:
I added a simple blinky project: 5ad8c5fddb014f

Closed 2018-03-28.

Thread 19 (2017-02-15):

Double the size of cell when print

kbumsik, 2017-02-15:
Our maze currently prints only a single character size cells. But it restricts expression our algorithms.
So we need to increase the size. Here is how our sample maze should look like (it replaces [a file simulation/1.txt](https://github.com/kbumsik/WolfieMouse/blob/master/simulation/maze_solving/1.txt)

```
 __ __ __ __ __ __ __ __ __ __ __ __ __ __ __ __
|  *  *  *  *  *  *  *  *  *  *  *  *  *  *  *  |
 ** ** ** ** ** ** ** ** ** ** ** ** ** ** ** **
|  *  *  *  *  *  *  *  *  *  *  *  *  *  *  *  |
 ** ** ** ** ** ** ** __ ** ** ** ** ** ** ** **
|  *  *  *  *  *  *  |  |  *  *  *  *  *  *  *  |
 __ __ __ __ __ __ __ .. ** ** ** ** ** ** ** **
|  .  .  .  .  .  .  .  |  *  *  *  *  *  *  *  |
 .. .. __ __ __ __ __ __ __ ** ** ** ** ** ** **
|  |  .  .  .  .  .  .  |  |  *  *  *  *  *  *  |
 .. .. __ __ __ __ __ __ .. ** ** ** ** ** ** **
|  |  .  .  .  .  .  .  .  |  *  *  *  *  *  *  |
 .. .. __ __ __ __ __ __ .. ** ** ** ** ** ** **
|  |  |  *  *  *  *  *  |  |  *  *  *  *  *  *  |
 .. .. ** ** ** ** ** __ .. ** ** ** ** ** ** **
|  |  |  *  *  *  *  |G .G |  *  *  *  *  *  *  |
 .. .. ** ** ** __ __ .. .. __ __ __ __ ** ** **
|  |  |  *  *  |  .  .G .G |  .  .  .  |  *  *  |
 .. .. __ __ __ .. __ __ __ __ __ __ .. ** ** **
|  |  .  .  .  |  .  .  .  .  |  .  |  |  *  *  |
 .. __ __ __ .. .. __ __ __ .. __ __ .. ** ** **
|  .  .  .  |  |  |  .  .  |  .  .  .  |  *  *  |
 __ __ __ .. .. .. __ __ __ .. __ __ .. ** ** **
|  .  .  .  |  |  .  .  .  .  .  .  |  |  *  *  |
 .. __ __ __ .. __ __ __ __ __ __ __ .. ** ** **
|  .  .  .  |  .  .  .  .  .  .  .  .  |  *  *  |
 __ __ __ __ .. __ __ __ __ __ __ __ __ ** ** **
|  .  .  .  .  |  *  *  *  *  |  .  |  *  *  *  |
 .. .. __ __ __ ** ** ** ** ** .. .. ** ** ** **
|  |  |  *  *  *  *  *  *  *  |  |  |  *  *  *  |
 .. .. __ __ __ __ __ __ __ __ .. __ ** ** ** **
|S |  .  .  .  .  .  .  .  .  .  |  *  *  *  *  |
 __ __ __ __ __ __ __ __ __ __ __ __ __ __ __ __
```

And when print with distance:
```
 __ __ __ __ __ __ __ __ __ __ __ __ __ __ __ __
|  *  *  *  *  *  *  *  *  *  *  *  *  *  *  *  |
 ** ** ** ** ** ** ** ** ** ** ** ** ** ** ** **
|  *  *  *  *  *  *  *  *  *  *  *  *  *  *  *  |
 ** ** ** ** ** ** ** __ ** ** ** ** ** ** ** **
|  *  *  *  *  *  *  |  |  *  *  *  *  *  *  *  |
 __ __ __ __ __ __ __ .. ** ** ** ** ** ** ** **
|  .  .  .  .  .  .  .  |  *  *  *  *  *  *  *  |
 .. .. __ __ __ __ __ __ __ ** ** ** ** ** ** **
|  |  .  .  .  .  .  .  |  |  *  *  *  *  *  *  |
 .. .. __ __ __ __ __ __ .. ** ** ** ** ** ** **
|  |  .  .  .  .  .  .  .  |  *  *  *  *  *  *  |
 .. .. __ __ __ __ __ __ .. ** ** ** ** ** ** **
|  |  |  *  *  *  *  *  |  |  *  *  *  *  *  *  |
 .. .. ** ** ** ** ** __ .. ** ** ** ** ** ** **
|  |15|  *  *  *  *  |G .G |  *  *  *  *  *  *  |
 .. .. ** ** ** __ __ .. .. __ __ __ __ ** ** **
|  |14|  *  *  |  .  .G .G |  .  .  .  |  *  *  |
 .. .. __ __ __ .. __ __ __ __ __ __ .. ** ** **
|  |13.12.11.10|  .  .  .  .  |  .  |  |  *  *  |
 .. __ __ __ .. .. __ __ __ .. __ __ .. ** ** **
|  .  .  .  |9 |  |  .  .  |  .  .  .  |  *  *  |
 __ __ __ .. .. .. __ __ __ .. __ __ .. ** ** **
|  .  .  .  |8 |  .  .  .  .  .  .  |  |  *  *  |
 .. __ __ __ .. __ __ __ __ __ __ __ .. ** ** **
|  .  .  .  |7 .  .  .  .  .  .  .  .  |  *  *  |
 __ __ __ __ .. __ __ __ __ __ __ __ __ ** ** **
|2 .3 .4 .5 .6 |  *  *  *  *  |  .  |  *  *  *  |
 .. .. __ __ __ ** ** ** ** ** .. .. ** ** ** **
|1 |  |  *  *  *  *  *  *  *  |  |  |  *  *  *  |
 .. .. __ __ __ __ __ __ __ __ .. __ ** ** ** **
|S |  .  .  .  .  .  .  .  .  .  |  *  *  *  *  |
 __ __ __ __ __ __ __ __ __ __ __ __ __ __ __ __
```

gonzagab, 2017-02-15:
#21 Check it out

kbumsik, 2017-02-19:
This issue is resolved. Thank you @gonzagab !

Closed 2017-02-19.

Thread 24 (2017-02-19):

Dynamic position of goal in maze

kbumsik, 2017-02-19:
@gonzagab
Currently we have maze of fixed 16x16, as we specified using `#define`. But we have a smaller maze in IEEE lab, This is okay in our code structure as the border of the maze will be considered as 'blocked wall' anyway and we can draw like that in the simulation. The problem is the position of goal is also fixed.
We should be able to define the position of goal using marking `G` in the maze file.

If anyone have question on the issue and our software. Just ask me here by commenting!

kbumsik, 2017-02-22:
We noticed that our code already doing well. I will double check it and then close the issue.

Closed 2017-03-05.

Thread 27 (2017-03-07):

Display Mouse's direction

kbumsik, 2017-03-07:
Currently `M` is displayed to indicate the position of the mouse in terminal. It would be better when we see current direction of the mouse.
However, ASCII code does not have arrows (e.g. ↑,↓,←,→) so we cannot print them.
Instead we could print `U` `D` `L` `R` to show direction. Maybe we can come up a better solution like `->` and `<-`.

Closed 2017-03-17.

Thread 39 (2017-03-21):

Hardware driver improvements

kbumsik, 2017-03-21:
Here are problems:
- [ ] : Uninitialized variables (`.bss`) is too much (almost 100k!)
- [ ] : Encoder is a little bit low-resolution. (around 200/rev) Speed is often measured in 0mm/s because our algorithm updates the encoder ever 1ms

Closed 2018-03-28.

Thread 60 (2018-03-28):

Global use of Range finder

kbumsik, 2018-03-28:
When look at [RealMouse.cc](https://github.com/kbumsik/WolfieMouse/blob/18e8a2ec4a3acf54753b23be55af6cc53a054e03/firmware/competition_wolfiemouse/RealMouse.cc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), we can see a use of global variable from [thread_control_loop.c](https://github.com/kbumsik/WolfieMouse/blob/18e8a2ec4a3acf54753b23be55af6cc53a054e03/firmware/src/board/wolfiemouse/thread_control_loop.c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). This is definitely not a good practice.

kbumsik, 2018-04-10:
I might need to use Event Groups in FreeRTOS for this feature.

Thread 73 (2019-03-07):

Adding logger breaks real-time constraints

kbumsik, 2019-03-07:
It appears that using `logger_log()` will delay the `control_loop` thread so that PID loop does is not triggered on time.
It looks like there is a problem with context switching.

kbumsik, 2019-03-10:
I fixed it by using vTaskDelay(1) instead of Systick Hook.

Closed 2019-03-10.

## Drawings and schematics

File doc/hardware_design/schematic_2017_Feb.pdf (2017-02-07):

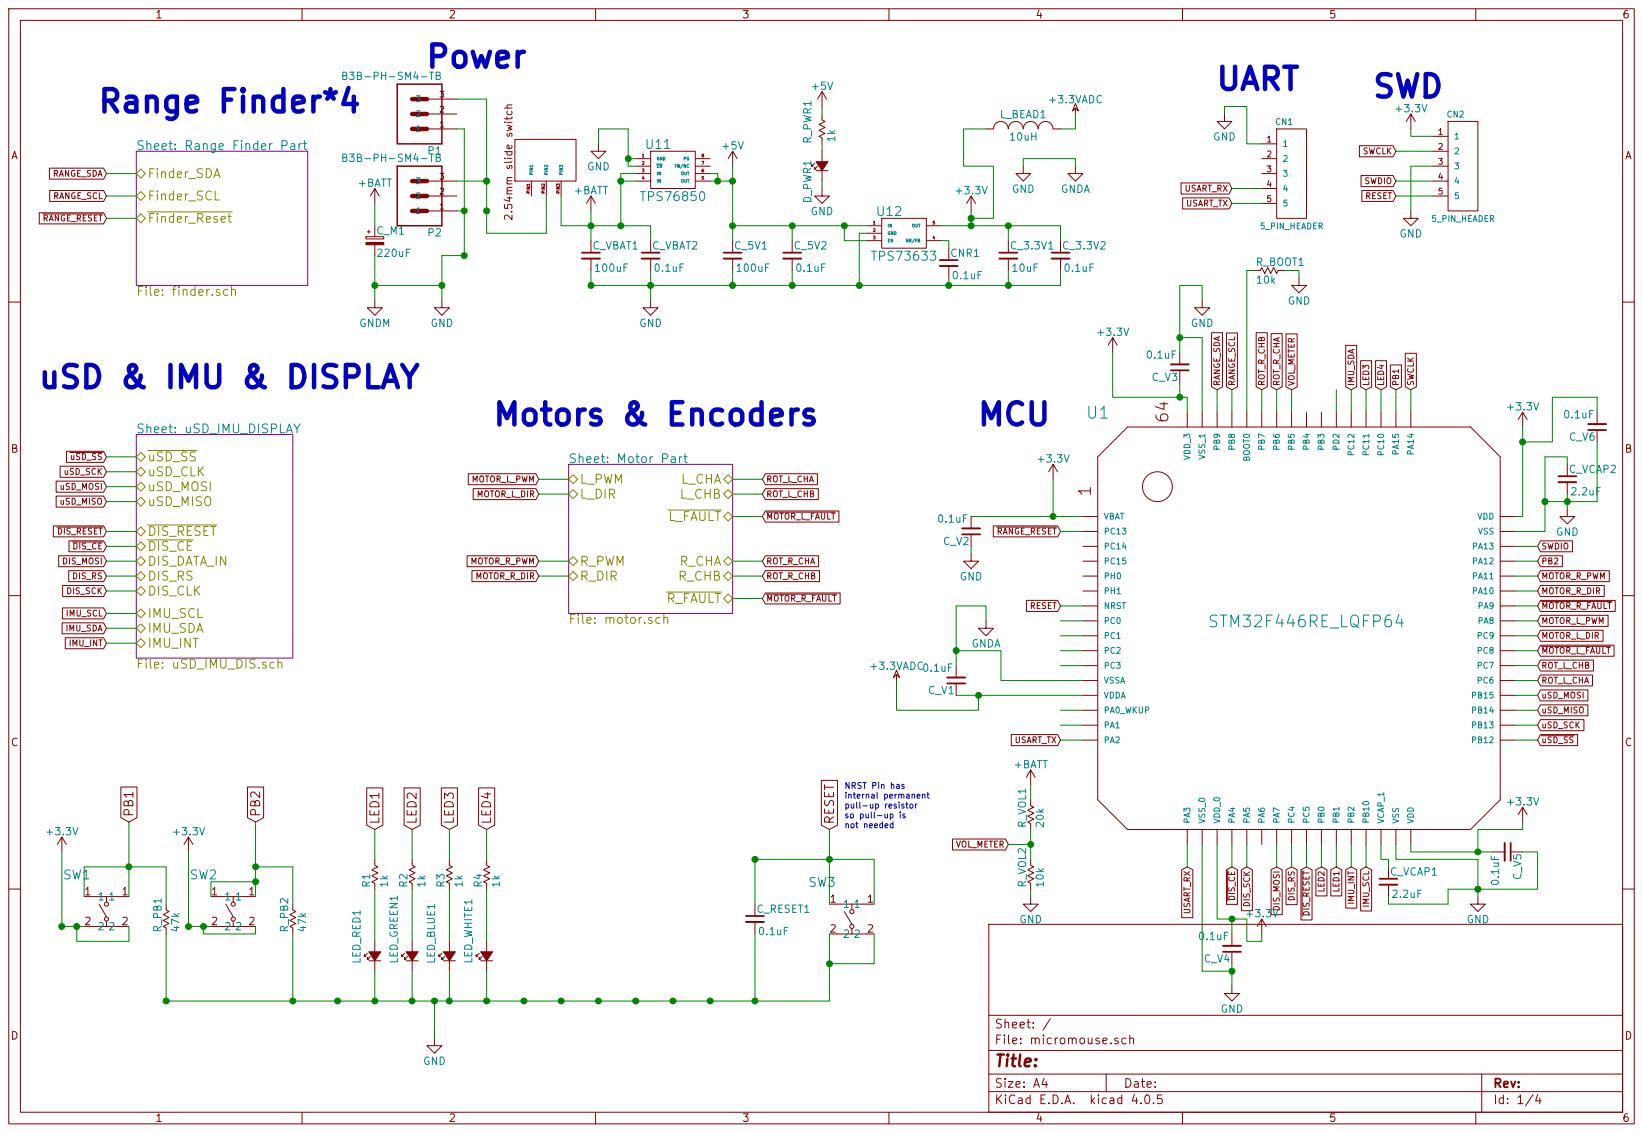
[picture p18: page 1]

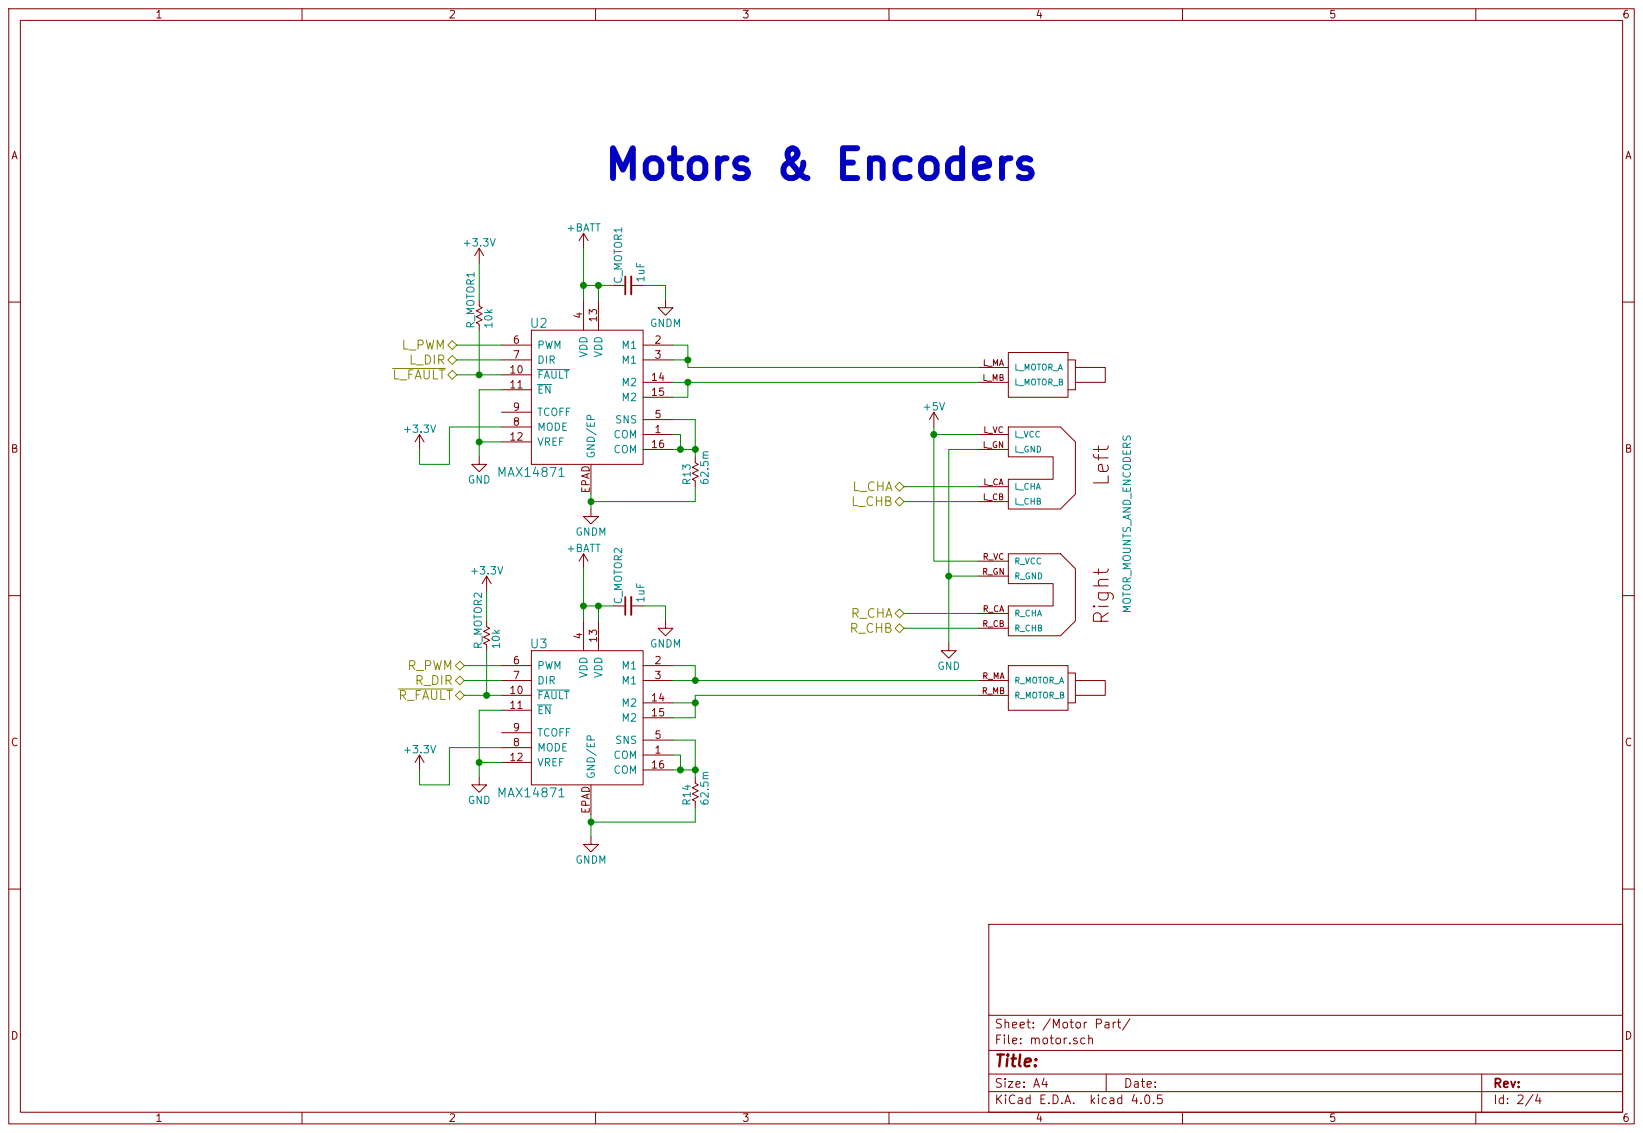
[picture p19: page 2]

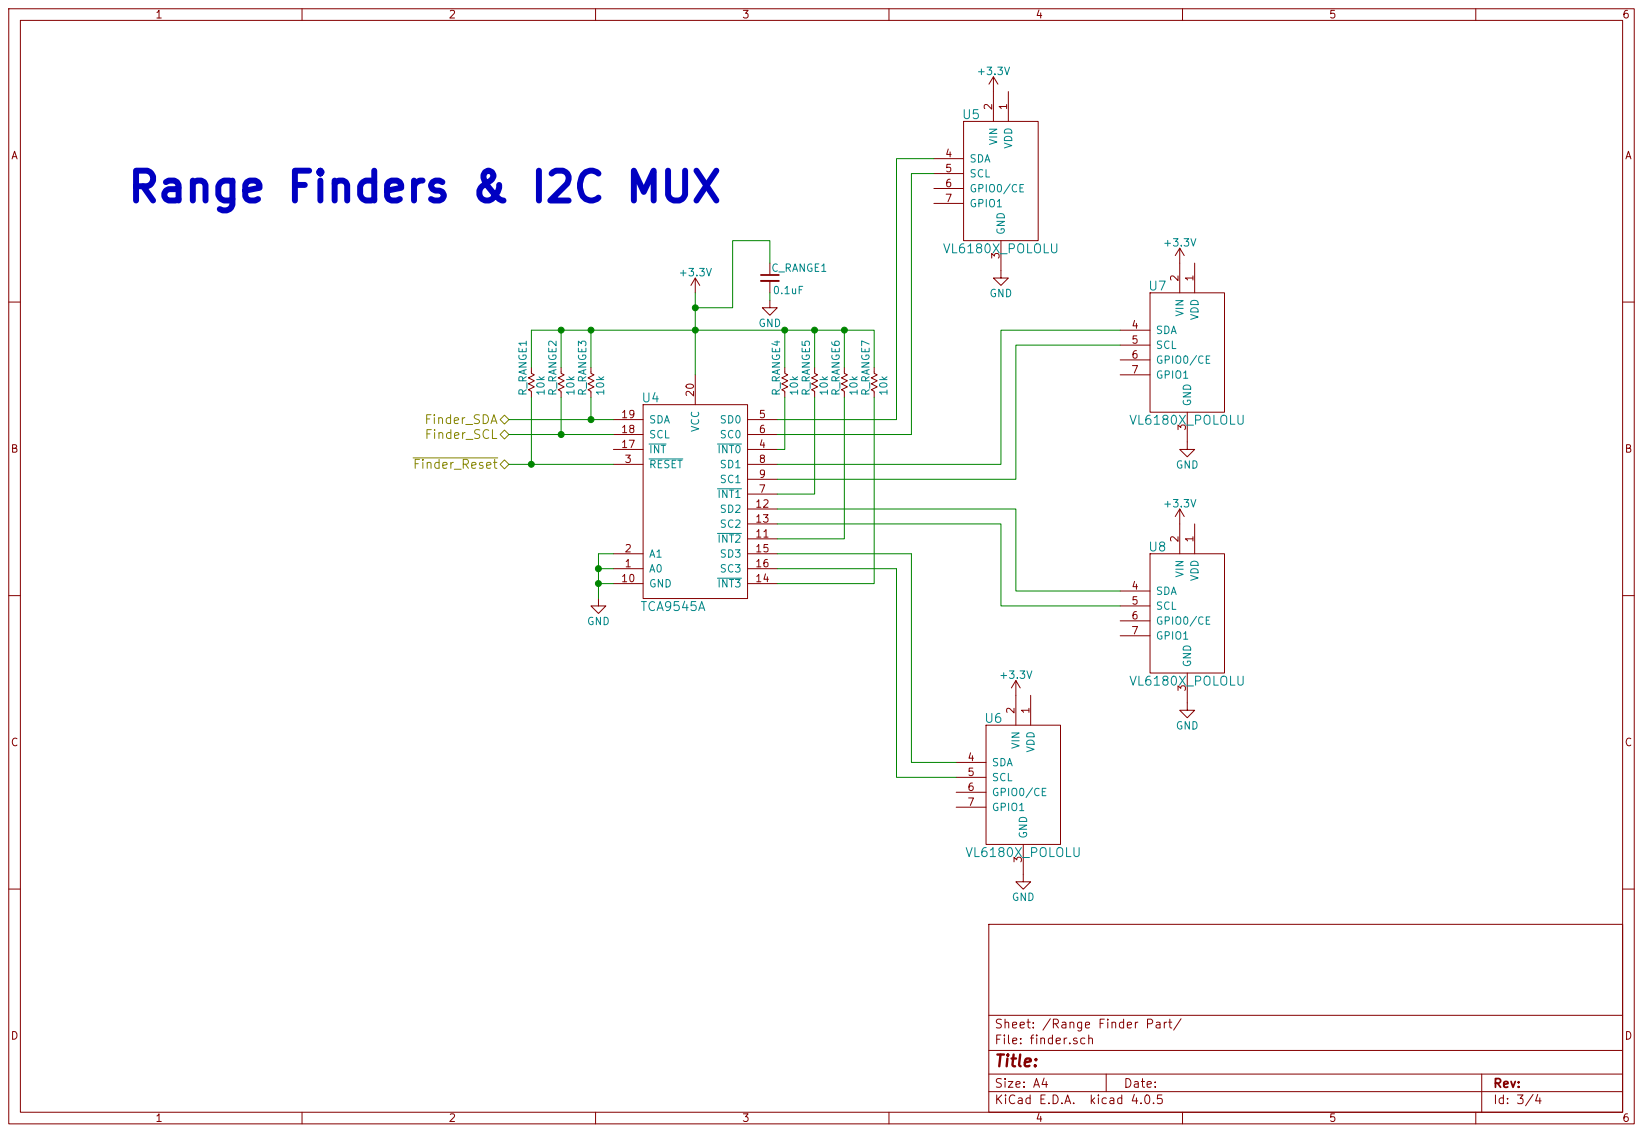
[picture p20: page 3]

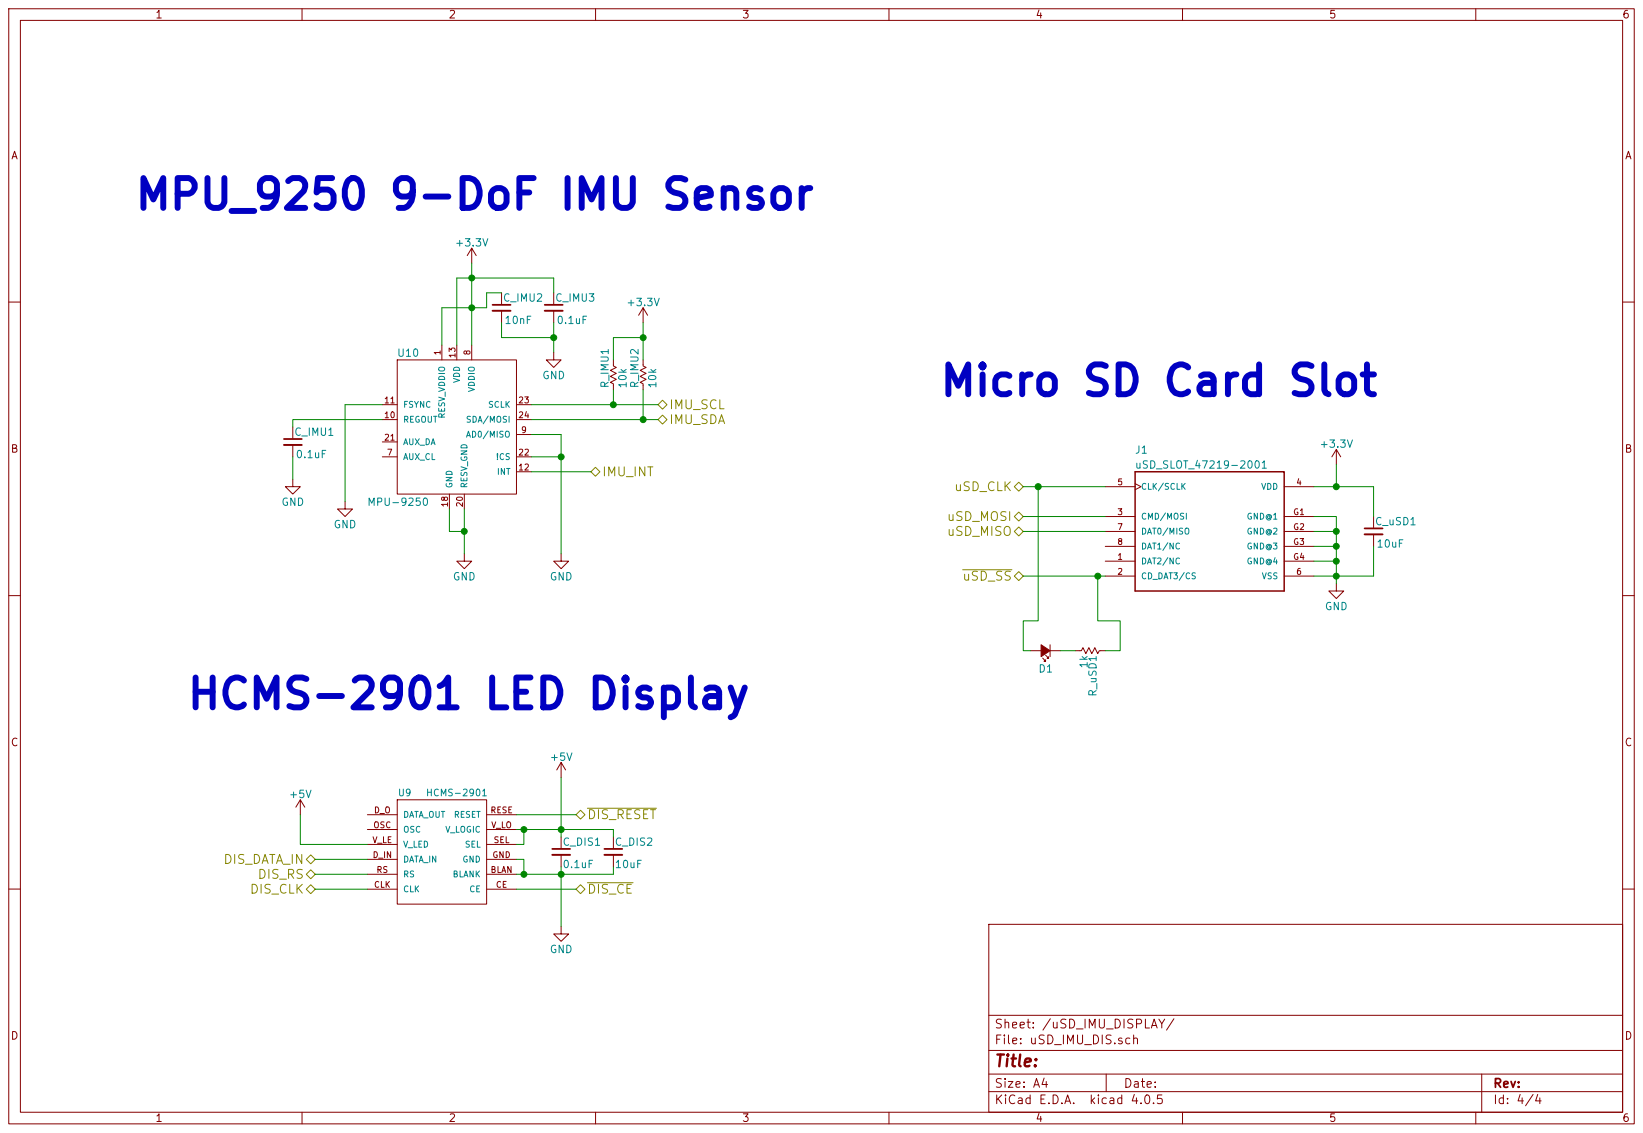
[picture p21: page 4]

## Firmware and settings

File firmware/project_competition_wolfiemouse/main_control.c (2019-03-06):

#include "main_control.h"
#include "thread_control_loop.h"
#include "config_measurements.h"
#include "motor.h"
#include "encoder.h"
#include "pid.h"
#include "range.h"
#include "logger.h"

/*******************************************************************************
 * Constants definition
 ******************************************************************************/
/* Set target PID speed */
#define TARGET_MOVE_FORWARD_SPEED_TRAN  (10)
#define TARGET_MOVE_FORWARD_SPEED_ROT   (0)

#define TARGET_PIVOT_SPEED_TRAN         (0)
#define TARGET_PIVOT_SPEED_ROT          (-30)

#define TARGET_SMOOTH_TURN_SPEED_TRAN   (15)
#define TARGET_SMOOTH_TURN_SPEED_ROT    (-30)

/* Set PID controller */
pid_value_t pid_tran_forwarding_value = {
        .kp = 35,
        .ki = 5, // 0.01
        .kd = 10
};

pid_value_t pid_rot_forwarding_value = {
            .kp = 3,
            .ki = 0,
            .kd = 400
};

pid_value_t pid_tran_rotating_value = {
        .kp = 35,
        .ki = 5, // 0.01
        .kd = 10
};

pid_value_t pid_rot_rotating_value = {
            .kp = 7,
            .ki = 0.1,
            .kd = 20
};

pid_value_t pid_tran_smooth_value = {
        .kp = 35,
        .ki = 5, // 0.01
        .kd = 10
};

pid_value_t pid_rot_smooth_value = {
            .kp = 30,
            .ki = 0,
            .kd = 20
};

/*******************************************************************************
 * Local data structure
 ******************************************************************************/
// Wheel state
enum wheel_direction {
    WHEEL_DISABLED, WHEEL_FORWARD, WHEEL_BACKWARD
};

struct wheel_status {
    enum wheel_direction left;
    enum wheel_direction right;
};

/*******************************************************************************
 * Driver and function declarations
 ******************************************************************************/
void do_nothing (struct main_pid *pid);
void move_from_back_to_start_center (struct main_pid *pid);
void move_forward_one_cell (struct main_pid *pid);
void move_forward_half_cell (struct main_pid *pid);
void pivot_left_90_degree (struct main_pid *pid);
void pivot_right_90_degree (struct main_pid *pid);
void turn_left_smooth (struct main_pid *pid);
void turn_right_smooth (struct main_pid *pid);
void set_pid_and_go (struct main_pid *pid);
void reset_pid_and_stop (struct main_pid *pid);

void (*const main_control_driver[])(struct main_pid *pid) = {
    do_nothing,                     // CMD_NOTHING
    move_from_back_to_start_center, // CMD_BACK_TO_SART_CENTER
    move_forward_one_cell,          // CMD_MOVE_FORWARD_ONE_CELL
    move_forward_half_cell,         // CMD_MOVE_FORWARD_HALF_CELL
    pivot_left_90_degree,           // CMD_PIVOT_LEFT_90_DEGREE
    pivot_right_90_degree,          // CMD_PIVOT_RIGHT_90_DEGREE
    turn_left_smooth,               // CMD_TURN_LEFT_SMOOTH
    turn_right_smooth,              // CMD_TURN_RIGHT_SMOOTH
    set_pid_and_go,                 // CMD_LOW_SET_PID_AND_GO
    reset_pid_and_stop,             // CMD_LOW_RESET_PID_AND_STOP
};

/*******************************************************************************
 * Common function definitions
 ******************************************************************************/
/* Control loops */
void loop_move_forward (struct main_pid *pid,
                        pid_value_t *pid_tran,
                        pid_value_t *pid_rot,
                        int32_t target_speed_tran,
                        int32_t target_speed_rot,
                        int16_t target_step_left,
                        int16_t target_step_right);
void loop_pivot (struct main_pid *pid,
                 pid_value_t *pid_tran,
                 pid_value_t *pid_rot,
                 int32_t target_speed_tran,
                 int32_t target_speed_rot,
                 int16_t target_step_left,
                 int16_t target_step_right);
void loop_smooth_trun (struct main_pid *pid,
                       pid_value_t *pid_tran,
                       pid_value_t *pid_rot,
                       int32_t target_speed_tran,
                       int32_t target_speed_rot,
                       int16_t target_step_left,
                       int16_t target_step_right);

/* etc. */
void update_steps_and_speed (struct step_data *total_step,
                             struct speed_data *speed);
void update_range (struct range_data *range);
void stop_motor (struct main_pid *pid);
int check_escape_condition (struct main_pid *pid,
                            struct step_data *total_step,
                            struct step_data *target_step,
                            struct wheel_status *target_wheel_dir);

/*******************************************************************************
 * Function definitions
 ******************************************************************************/
void do_nothing (struct main_pid *pid)
{
    // Do nothing. Literally.
}

void move_from_back_to_start_center (struct main_pid *pid)
{
    loop_move_forward (pid,
                       &pid_tran_forwarding_value,
                       &pid_rot_forwarding_value,
                       TARGET_MOVE_FORWARD_SPEED_TRAN,
                       TARGET_MOVE_FORWARD_SPEED_ROT,
                       MEASURE_STEPS_BACK_TO_START_CENTER,
                       MEASURE_STEPS_BACK_TO_START_CENTER);
}

void move_forward_one_cell (struct main_pid *pid)
{
    loop_move_forward (pid,
                       &pid_tran_forwarding_value,
                       &pid_rot_forwarding_value,
                       TARGET_MOVE_FORWARD_SPEED_TRAN,
                       TARGET_MOVE_FORWARD_SPEED_ROT,
                       MEASURE_STEPS_PER_CELL,
                       MEASURE_STEPS_PER_CELL);
}

void move_forward_half_cell (struct main_pid *pid)
{
    loop_move_forward (pid,
                       &pid_tran_forwarding_value,
                       &pid_rot_forwarding_value,
                       TARGET_MOVE_FORWARD_SPEED_TRAN,
                       TARGET_MOVE_FORWARD_SPEED_ROT,
                       MEASURE_STEPS_PER_CELL / 2,
                       MEASURE_STEPS_PER_CELL / 2);
}

void pivot_left_90_degree (struct main_pid *pid)
{
    loop_pivot (pid,
                &pid_tran_rotating_value,
                &pid_rot_rotating_value,
                TARGET_PIVOT_SPEED_TRAN,
                TARGET_PIVOT_SPEED_ROT,
                -MEASURE_STEPS_90DEG_CCW,
                MEASURE_STEPS_90DEG_CCW);
}

void pivot_right_90_degree (struct main_pid *pid)
{
    loop_pivot (pid,
                &pid_tran_rotating_value,
                &pid_rot_rotating_value,
                TARGET_PIVOT_SPEED_TRAN,
                -TARGET_PIVOT_SPEED_ROT,
                MEASURE_STEPS_90DEG_CW,
                -MEASURE_STEPS_90DEG_CW);
}

void turn_left_smooth (struct main_pid *pid)
{
    loop_smooth_trun (pid,
                      &pid_tran_smooth_value,
                      &pid_rot_smooth_value,
                      TARGET_SMOOTH_TURN_SPEED_TRAN,
                      TARGET_SMOOTH_TURN_SPEED_ROT,
                      MEASURE_STEPS_SMOOTH_L_LEFT,
                      MEASURE_STEPS_SMOOTH_L_RIGHT);
}

void turn_right_smooth (struct main_pid *pid)
{
    loop_smooth_trun (pid,
                      &pid_tran_smooth_value,
                      &pid_rot_smooth_value,
                      TARGET_SMOOTH_TURN_SPEED_TRAN,
                      -TARGET_SMOOTH_TURN_SPEED_ROT,
                      MEASURE_STEPS_SMOOTH_R_LEFT,
                      MEASURE_STEPS_SMOOTH_R_RIGHT);
}

void set_pid_and_go (struct main_pid *pid)
{
    // Not used
}

void reset_pid_and_stop (struct main_pid *pid)
{
    stop_motor(pid);
}

/*******************************************************************************
 * Common function definitions (control loop)
 ******************************************************************************/
void loop_move_forward (struct main_pid *pid,
                        pid_value_t *pid_tran,
                        pid_value_t *pid_rot,
                        int32_t target_speed_tran,
                        int32_t target_speed_rot,
                        int16_t target_step_left,
                        int16_t target_step_right)
{
    struct range_data *range = &g_range;    // Range finder value
    struct speed_data speed;    // Speed value
    // TODO: Prevent underflow/overflow.
    struct step_data total_step = { // Accumulated step (distance) values
        .left = MEASURE_ENCODER_DEFAULT,
        .right = MEASURE_ENCODER_DEFAULT,
    };
    struct step_data target_step;   // Target step (distance) values
    struct wheel_status target_wheel_dir; // Target wheel direction

    // Load PID profiles
    pid_set_pid(&pid->tran, pid_tran);
    pid_set_pid(&pid->rot, pid_rot);

    // Set target speed values
    pid_input_setpoint(&pid->tran, target_speed_tran);
    pid_input_setpoint(&pid->rot, target_speed_rot);

    // Set target steps (or travel distance)
    target_step.left = MEASURE_ENCODER_DEFAULT + target_step_left;
    target_step.right = MEASURE_ENCODER_DEFAULT + target_step_right;

    // Set wheel directions
    target_wheel_dir.left = WHEEL_FORWARD;
    target_wheel_dir.right = WHEEL_FORWARD;

    while (1) {
        thread_control_wait_until_1ms();
        update_steps_and_speed(&total_step, &speed);
        update_range(range);

        // if it is too close stop
        if ((range->front > MEASURE_RANGE_F_NEAR_DETECT) ||
            (range->front_right > MEASURE_RANGE_F_NEAR_DETECT)) {
            stop_motor(pid);
            break;
        }

        /* compute PID */
        // calculate errorT
        int32_t feedback_T = (speed.left + speed.right) / 2;
        // calculate errorR
        int32_t feedback_R;
        if((range->left > (MEASURE_RANGE_L_MIN_DETECT))
                            && (range->right > MEASURE_RANGE_R_MIN_DETECT) ) {
            // If both range are within wall detecting distance,
            // Use range sensor to get rotational error
            feedback_R = (range->right - range->left - MEASURE_RANGE_R_OFFSET) / 10;
        } else if (range->left > (MEASURE_RANGE_L_MIN_DETECT + 50)) {
            // If only left side is within range
            // use the middle value of the right range
            feedback_R = (MEASURE_RANGE_R_M_DETECT - range->left) / 10;
        } else if (range->right > (MEASURE_RANGE_R_MIN_DETECT + 50)) {
            // If only right side is within range
            // use the middle value of the left range
            feedback_R = (range->right - MEASURE_RANGE_L_M_DETECT) / 10;
        } else {
            // in open space, use rotary encoder
            feedback_R = speed.diff;
        }
        // Calculate PID outputs
        int32_t outputT = pid_compute(&pid->tran, feedback_T);
        int32_t outputR = pid_compute(&pid->rot, feedback_R);

        // Apply to the motor
        motor_speed_permyriad(CH_LEFT, outputT + outputR);
        motor_speed_permyriad(CH_RIGHT, outputT - outputR);
        motor_start(CH_BOTH);

        logger_log(pid, range, &total_step, &speed, outputT, outputR);

        if (check_escape_condition(pid, &total_step, &target_step,
                                   &target_wheel_dir)) {
            break;
        }
    }
}

void loop_pivot (struct main_pid *pid,
                 pid_value_t *pid_tran,
                 pid_value_t *pid_rot,
                 int32_t target_speed_tran,
                 int32_t target_speed_rot,
                 int16_t target_step_left,
                 int16_t target_step_right)
{
    struct speed_data speed;    // Speed value
    // TODO: Prevent underflow/overflow.
    struct step_data total_step = { // Accumulated step (distance) values
        .left = MEASURE_ENCODER_DEFAULT,
        .right = MEASURE_ENCODER_DEFAULT,
    };
    struct step_data target_step;   // Target step (distance) values
    struct wheel_status target_wheel_dir; // Target wheel direction

    // Load PID profiles
    pid_set_pid(&pid->tran, pid_tran);
    pid_set_pid(&pid->rot, pid_rot);

    // Reset PID, or reset accumulated (integrated) speed error
    pid_reset(&pid->tran);
    pid_reset(&pid->rot);

    // Set target speed values
    pid_input_setpoint(&pid->tran, target_speed_tran);
    pid_input_setpoint(&pid->rot, target_speed_rot);

    // Set target steps (or travel distance)
    target_step.left = MEASURE_ENCODER_DEFAULT + target_step_left;
    target_step.right = MEASURE_ENCODER_DEFAULT + target_step_right;

    // Set wheel directions
    target_wheel_dir.left = (target_step_left > 0) ? WHEEL_FORWARD : WHEEL_BACKWARD;
    target_wheel_dir.right = (target_step_right > 0) ? WHEEL_FORWARD : WHEEL_BACKWARD;

    while (1) {
        thread_control_wait_until_1ms();
        update_steps_and_speed(&total_step, &speed);

        /* Calculate PID */
        // calculate errorT
        int32_t feedback_T = (speed.left + speed.right) / 2;
        // calculate errorR
        int32_t feedback_R = speed.diff;
        // Calculate PID outputs
        int32_t outputT = pid_compute(&pid->tran, feedback_T);
        int32_t outputR = pid_compute(&pid->rot, feedback_R);

        // Apply to the motor
        motor_speed_permyriad(CH_LEFT, outputT + outputR);
        motor_speed_permyriad(CH_RIGHT, outputT - outputR);
        motor_start(CH_BOTH);

        logger_log(pid, NULL, &total_step, &speed, outputT, outputR);

        if (check_escape_condition(pid, &total_step, &target_step,
                                    &target_wheel_dir)) {
            stop_motor(pid);
            break;
        }
    }
}

void loop_smooth_trun (struct main_pid *pid,
                       pid_value_t *pid_tran,
                       pid_value_t *pid_rot,
                       int32_t target_speed_tran,
                       int32_t target_speed_rot,
                       int16_t target_step_left,
                       int16_t target_step_right)
{
    struct speed_data speed;    // Speed value
    // TODO: Prevent underflow/overflow.
    struct step_data total_step = { // Accumulated step (distance) values
        .left = MEASURE_ENCODER_DEFAULT,
        .right = MEASURE_ENCODER_DEFAULT,
    };
    struct step_data target_step;   // Target step (distance) values
    struct wheel_status target_wheel_dir; // Target wheel direction

    // Load PID profiles
    pid_set_pid(&pid->tran, pid_tran);
    pid_set_pid(&pid->rot, pid_rot);

    // Reset PID, or reset accumulated (integrated) speed error
    pid_reset(&pid->tran);
    pid_reset(&pid->rot);

    // Set target speed values
    pid_input_setpoint(&pid->tran, target_speed_tran);
    pid_input_setpoint(&pid->rot, target_speed_rot);

    // Set target steps (or travel distance)
    target_step.left = MEASURE_ENCODER_DEFAULT + target_step_left;
    target_step.right = MEASURE_ENCODER_DEFAULT + target_step_right;

    // Set wheel directions
    target_wheel_dir.left = WHEEL_FORWARD;
    target_wheel_dir.right = WHEEL_FORWARD;

    while (1) {
        thread_control_wait_until_1ms();
        update_steps_and_speed(&total_step, &speed);

        /* Calculate PID */
        // calculate errorT
        int32_t feedback_T = (speed.left + speed.right) / 2;
        // calculate errorR
        int32_t feedback_R = speed.diff;
        // Calculate PID outputs
        int32_t outputT = pid_compute(&pid->tran, feedback_T);
        int32_t outputR = pid_compute(&pid->rot, feedback_R);

        // Apply to the motor
        motor_speed_permyriad(CH_LEFT, outputT + outputR);
        motor_speed_permyriad(CH_RIGHT, outputT - outputR);
        motor_start(CH_BOTH);

        logger_log(pid, NULL, &total_step, &speed, outputT, outputR);

        if (check_escape_condition(pid, &total_step, &target_step,
                                    &target_wheel_dir)) {
            break;
        }
    }
}

/*******************************************************************************
 * Common function definitions (etc.)
 ******************************************************************************/
void update_steps_and_speed (struct step_data *total_step, struct speed_data *speed)
{
    struct encoder_data step;
    // Update steps from rotary encoders
    encoder_get(&step, ENCODER_CH_BOTH);
    encoder_reset(ENCODER_CH_BOTH); // Then reset
    // update speed
    speed->left = (step.left - MEASURE_ENCODER_DEFAULT);// * CONFIG_LEN_PER_CNT;
    speed->right = (step.right - MEASURE_ENCODER_DEFAULT);// * CONFIG_LEN_PER_CNT;
    speed->diff = speed->left - speed->right;
    // Accumulate steps
    total_step->left += speed->left;
    total_step->right += speed->right;
}

void update_range (struct range_data *range)
{
    range_get(range, RANGE_CH_ALL);

    if (range->left > MEASURE_RANGE_L_MAX_DETECT) {
        range->left = MEASURE_RANGE_L_MAX_DETECT;
    }

    if (range->right > MEASURE_RANGE_R_MAX_DETECT) {
        range->right = MEASURE_RANGE_R_MAX_DETECT;
    }
}

void stop_motor (struct main_pid *pid)
{
    motor_speed_percent(CH_BOTH, 0);
    motor_start(CH_BOTH);
    pid_reset(&pid->tran);
    pid_reset(&pid->rot);
}

int check_escape_condition (struct main_pid *pid,
                            struct step_data *total_step,
                            struct step_data *target_step,
                            struct wheel_status *target_wheel_dir)
{
    /* Escape condition */
    // update both wheels
    // left
    if (target_wheel_dir->left == WHEEL_FORWARD) {
        if (total_step->left > target_step->left) {
            target_wheel_dir->left = WHEEL_DISABLED;
        }
    } else if (target_wheel_dir->left == WHEEL_BACKWARD) {
        if (total_step->left < target_step->left) {
            target_wheel_dir->left = WHEEL_DISABLED;
        }
    }

    // right
    if (target_wheel_dir->right == WHEEL_FORWARD) {
        if (total_step->right > target_step->right) {
            target_wheel_dir->right = WHEEL_DISABLED;
        }
    } else if (target_wheel_dir->right == WHEEL_BACKWARD) {
        if (total_step->right < target_step->right) {
            target_wheel_dir->right = WHEEL_DISABLED;
        }
    }

    // if both wheels are completed then a command is complete
    if ((target_wheel_dir->left == WHEEL_DISABLED) &&
        (target_wheel_dir->right == WHEEL_DISABLED)) {
        // Escape loop
        return 1;
    }
    return 0;
}

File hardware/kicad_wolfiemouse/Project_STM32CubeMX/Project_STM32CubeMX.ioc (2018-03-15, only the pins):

Mcu.UserName=STM32F446RETx
PA0-WKUP.GPIO_Label=EMITTER_L
PA0-WKUP.Signal=GPIO_Output
PA1.GPIO_Label=EMITTER_FL
PA1.Signal=GPIO_Output
PA10.GPIO_Label=motorPIN_R_DIR
PA10.Signal=GPIO_Output
PA11.GPIO_Label=motorPIN_R_PWM
PA11.Signal=S_TIM1_CH4
PA12.GPIO_Label=PB2_PIN
PA12.Signal=GPXTI12
PA13.GPIO_Label=TMS
PA13.Signal=SYS_JTMS-SWDIO
PA14.GPIO_Label=TCK
PA14.Signal=SYS_JTCK-SWCLK
PA15.GPIO_Label=PB1_PIN
PA15.Signal=GPXTI15
PA2.GPIO_Label=USART_TX
PA2.Signal=USART2_TX
PA3.GPIO_Label=USART_RX
PA3.Signal=USART2_RX
PA4.GPIO_Label=disPIN_CE_BAR
PA4.Signal=GPIO_Output
PA5.GPIO_Label=disPIN_SCK
PA5.Signal=SPI1_SCK
PA6.GPIO_Label=BATT_LEVEL
PA6.Signal=ADCx_IN6
PA7.GPIO_Label=disPIN_MOSI
PA7.Signal=SPI1_MOSI
PA8.GPIO_Label=motorPIN_L_PWM
PA8.Signal=S_TIM1_CH1
PA9.GPIO_Label=motorPIN_R_FAULT_BAR
PA9.Signal=S_TIM1_CH2
PB0.GPIO_Label=LED1_PIN
PB0.Signal=GPIO_Output
PB1.GPIO_Label=LED2_PIN
PB1.Signal=GPIO_Output
PB12.GPIO_Label=usdPIN_SS_BAR
PB12.Signal=SPI2_NSS
PB13.GPIO_Label=usdPIN_SCK
PB13.Signal=SPI2_SCK
PB14.GPIO_Label=usdPIN_MISO
PB14.Signal=SPI2_MISO
PB15.GPIO_Label=usdPIN_MOSI
PB15.Signal=SPI2_MOSI
PB3.GPIO_Label=SWO
PB3.Signal=SYS_JTDO-SWO
PB4.GPIO_Label=counterPIN_R_CHA
PB4.Signal=S_TIM3_CH1
PB5.GPIO_Label=counterPIN_R_CHB
PB5.Signal=S_TIM3_CH2
PB7.GPIO_Label=imu_INT
PB7.Signal=GPXTI7
PB8.GPIO_Label=imuPIN_SCL
PB8.Signal=I2C1_SCL
PB9.GPIO_Label=imuPIN_SDA
PB9.Signal=I2C1_SDA
PC0.GPIO_Label=RECV_FR
PC0.Signal=ADCx_IN10
PC1.GPIO_Label=RECV_R
PC1.Signal=ADCx_IN11
PC10.GPIO_Label=LED4_PIN
PC10.Signal=GPIO_Output
PC11.GPIO_Label=LED3_PIN
PC11.Signal=GPIO_Output
PC13.GPIO_Label=EMITTER_FR
PC13.Signal=GPIO_Output
PC14-OSC32_IN.GPIO_Label=EMITTER_R
PC14-OSC32_IN.Signal=GPIO_Output
PC15-OSC32_OUT.Signal=RCC_OSC32_OUT
PC2.GPIO_Label=RECV_L
PC2.Signal=ADCx_IN12
PC3.GPIO_Label=RECV_FL
PC3.Signal=ADCx_IN13
PC4.GPIO_Label=disPIN_RS
PC4.Signal=GPIO_Output
PC5.GPIO_Label=disPIN_RESET_BAR
PC5.Signal=GPIO_Output
PC6.GPIO_Label=counterPIN_L_CHA
PC6.Signal=S_TIM8_CH1
PC7.GPIO_Label=counterPIN_L_CHB
PC7.Signal=S_TIM8_CH2
PC8.GPIO_Label=motorPIN_L_FAULT_BAR
PC8.Signal=GPXTI8
PC9.GPIO_Label=motorPIN_L_DIR
PC9.Signal=GPIO_Output
PH0-OSC_IN.Signal=RCC_OSC_IN
PH1-OSC_OUT.Signal=RCC_OSC_OUT

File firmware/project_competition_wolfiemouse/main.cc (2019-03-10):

// In the same folder
#include "main_fsm_table.hpp"
#include "logger_thread.h"
#include "button.hpp"

// FreeRTOS
#include "FreeRTOS.h"
#include "portable.h" // TODO: Delete
#include "task.h"
#include "queue.h"
#include "semphr.h"

#include "config_measurements.h"

// KB library
#include "tick.h"
#include "trace.h"
#include "gpio.h"
#include "hcms_290x_display.h"
#include "terminal.h"
#include "encoder.h"
#include "system_config.h"
#include "control_loop_thread.h"
#include "cmd.h"
#include "range.h"

// Maze solver
#include "MouseController.hpp"
#include "IOInterface.hpp"
#include "RealMouse.hpp"
#include "StdIO.hpp"
#include "FlashIO.hpp"

// Define message base. This is used for KB_DEBUG_MSG()
#ifdef KB_MSG_BASE
#    undef KB_MSG_BASE
#    define KB_MSG_BASE "Main"
#endif

/*******************************************************************************
 * Function declarations and local variables
 ******************************************************************************/
// Maze solver
static void _maze_solver_run(void (*wait_func)(MouseController *mouse));
static void _wait_for_button(MouseController *mouse);

// Thread declarations
static void _thread_main(void *pvParameters);

/*******************************************************************************
 * FSM action function
 ******************************************************************************/
/**
 * @brief Competition mode. This task is used for actual competition.
 */
void task_1(void)
{
    /* Give time to get ready */
    hcms_290x_matrix("RDY.");
    for (int i = 0; i < 6; i++) {
        gpio_toggle(LED2_PORT, LED2_PIN);
        delay_ms(500);
    }
    hcms_290x_matrix("PRSS");

    // wait for button pressed
    button_b1_b2_wait();

    hcms_290x_matrix("Go");
    delay_ms(1000);
    hcms_290x_matrix("    ");   // We should print empty spaces
                                // in order to save battery

    /* Go to main algorithm */
    _maze_solver_run(NULL);
}

/**
 * @brief Remote algorithm debugging mode. You can control the mouse
 *        step-by-step using serial console.
 */
void task_2(void)
{
    /* Not implemented */
    hcms_290x_matrix("Non2");
    delay_ms(2000);

    /* Give time to get ready */
    hcms_290x_matrix("PRSS");

    // wait for button pressed
    button_b1_b2_wait();

    hcms_290x_matrix("Go");
    delay_ms(1000);
    hcms_290x_matrix("    ");   // We should print empty spaces
                                // in order to save battery

    /* Go to main algorithm */
    _maze_solver_run(_wait_for_button);
}

/**
 * @brief Use front sensors to adjust micromouse.
 *        See https://www.youtube.com/watch?v=6PKUbhkdqWk
 */
void task_3(void)
{
    /* Not implemented */
    hcms_290x_matrix("Non3");
    delay_ms(2000);
}

/**
 * @brief Forward movement debugging mode. Mouse will move forward for 4 cells.
 */
void task_4(void)
{
    hcms_290x_matrix("Non4");
    delay_ms(2000);

    // Move
    cmd_polling(CMD_MOVE_FORWARD_ONE_CELL);
    cmd_polling(CMD_MOVE_FORWARD_ONE_CELL);
    cmd_polling(CMD_MOVE_FORWARD_ONE_CELL);
    cmd_polling(CMD_MOVE_FORWARD_ONE_CELL);
    cmd_polling(CMD_MOVE_FORWARD_ONE_CELL);
    cmd_polling(CMD_MOVE_FORWARD_ONE_CELL);
    cmd_low_pid_reset_and_stop(NULL);
}

/**
 * @brief Pivot-left debugging mode. Mouse will pivot left.
 */
void task_5(void)
{
    hcms_290x_matrix("Non5");
    delay_ms(1000);

    // Pivot
    cmd_polling(CMD_PIVOT_LEFT_90_DEGREE);
    cmd_low_pid_reset_and_stop(NULL);

    // Pivot 180 degree
    delay_ms(1000);
    cmd_polling(CMD_PIVOT_LEFT_90_DEGREE);
    cmd_low_pid_reset_and_stop(NULL);
    delay_ms(1000);
    cmd_polling(CMD_PIVOT_LEFT_90_DEGREE);
    cmd_low_pid_reset_and_stop(NULL);
    delay_ms(1000);
}

/**
 * @brief Pivot-right debugging mode. Mouse will pivot left.
 */
void task_6(void)
{
    hcms_290x_matrix("Non6");
    delay_ms(2000);

    // Pivot
    cmd_polling(CMD_PIVOT_RIGHT_90_DEGREE);
    cmd_low_pid_reset_and_stop(NULL);

    // Pivot 180 degree
    delay_ms(1000);
    cmd_polling(CMD_PIVOT_RIGHT_90_DEGREE);
    cmd_low_pid_reset_and_stop(NULL);
    delay_ms(1000);
    cmd_polling(CMD_PIVOT_RIGHT_90_DEGREE);
    cmd_low_pid_reset_and_stop(NULL);
    delay_ms(1000);
}

/*******************************************************************************
 * Maze_solver
 ******************************************************************************/
static void _maze_solver_run(void (*wait_func)(MouseController *mouse))
{
    // Maze solver state
    enum {
        goGoal  = 0,
        goStart = 1,
        explore = 2
    } mouseState = goGoal;

    // Create virtual mouse hardware for simulation
    static FlashIO flashIO;
    static StdIO printIO(false);
    static RealMouse realmouse;
    static MouseController mouse(NULL, &flashIO, &printIO,
            (FinderInterface*) &realmouse, (MoverInterface*) &realmouse);

    /* First just print maze */
    mouse.printMaze();

    range_get(&g_range, RANGE_CH_ALL); // To prevent the maze solver get wrong values

    while (true) {
        //Finite State Machine
        if (mouse.allDestinationsReached()) {
            switch (mouseState) {
            case goGoal:
                mouseState = explore;
                mouse.makeRandomDest(4);
                break;
            case explore:
                mouseState = goStart;
                mouse.makeStartAsDest();
                break;
            case goStart:
                mouseState = goGoal;
                mouse.makeGoalAsDest();
                break;
            default:
                //printf("Invalid state");
                break;
            }
        } else {
            if (!mouse.scanAndMove(wait_func)) {
                goto end;
            }
        }
        taskYIELD();
    }

end:
    return;
}

static void _wait_for_button(MouseController *mouse)
{
    char buffer[80];
    char *keyinput = buffer;
    char key;

    // Stop the mouse completely and print the maze and the information.
    cmd_low_pid_reset_and_stop(NULL);
    mouse->printMaze();
    puts("please input a command");
    puts("n:next, q: save and restart, p: print stack");
    fflush(stdout);

    while (true) {
        if (!terminal_gets(keyinput)) {
            // TODO: why it gets error? It seems to get error and sucess back and forth.
            // puts("Error!");
        }
        key = keyinput[0];
        keyinput[0] = ' ';
        if (key == 'n') {
            break;
        } else if (key == 'q') {
            goto save_and_exit;
        } else if (key == 'p') {
            mouse->printPathStack();
            fflush(stdout);
        } else {
            continue;
        }
        taskYIELD();
    }
    return;
save_and_exit:
    // Save it to flash
    mouse->saveMazeFile(NULL);
    puts("Maze saved to flash");
    puts("Good Bye!");
    exit(0);
    return;
}
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

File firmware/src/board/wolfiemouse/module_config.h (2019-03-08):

/*
 * module_config.h
 *
 *  Created on: Oct 26, 2016
 *      Author: Bumsik Kim
 */

#ifndef BSP_WOLFIEMOUSE_KB_MODULE_CONFIG_H_
#define BSP_WOLFIEMOUSE_KB_MODULE_CONFIG_H_

// Push button settings
#define B1_PORT 		PORTB
#define B1_PIN 			PIN_14

#define B2_PORT 		PORTB
#define B2_PIN 			PIN_15

// LED settings
#define LED1_PORT	PORTB
#define LED1_PIN	PIN_1

#define LED2_PORT	PORTB
#define LED2_PIN	PIN_0

#define LED3_PORT	PORTB
#define LED3_PIN	PIN_2

#define LED4_PORT	PORTB
#define LED4_PIN	PIN_10
#define LED5_PORT	PORTB
#define LED5_PIN	PIN_12

#define LED6_PORT	PORTB
#define LED6_PIN	PIN_13

// Terminal settings
#define TERMINAL_UART			USART2
#define TERMINAL_BAUD_RATE		115200 // 9600, 115200, or 460800

#define TERMINAL_TX_PORT 		GPIOA
#define TERMINAL_TX_PIN 		GPIO_PIN_2

#define TERMINAL_RX_PORT 		GPIOA
#define TERMINAL_RX_PIN 		GPIO_PIN_3


// HCMS_290X settings
#define HCMS_290X_SPI			SPI1

#define HCMS_290X_RS_PORT		PORTC
#define HCMS_290X_RS_PIN		PIN_4

#define HCMS_290X_RESET_PORT 	PORTC
#define HCMS_290X_RESET_PIN		PIN_5

#define HCMS_290X_CE_PORT		PORTA
#define HCMS_290X_CE_PIN		PIN_4

#define HCMS_290X_MOSI_PORT 	PORTA
#define HCMS_290X_MOSI_PIN		PIN_7

#define HCMS_290X_SCK_PORT		PORTA
#define HCMS_290X_SCK_PIN		PIN_5


// Motor
#define MOTOR_LEFT_PWM_PORT PORTA
#define MOTOR_LEFT_PWM_PIN  PIN_8

#define MOTOR_RIGHT_PWM_PORT PORTA
#define MOTOR_RIGHT_PWM_PIN  PIN_11

// Encoder
// Left encoder
#define ENCODER_L_TIMER     KB_ENCODER_TIM8
#define ENCODER_L_CHA_PORT  PORTC
#define ENCODER_L_CHA_PIN   PIN_6

#define ENCODER_L_CHB_PORT  PORTC
#define ENCODER_L_CHB_PIN   PIN_7
#define ENCODER_L_PIN_PULLUP NOPULL
// Right encoder
#define ENCODER_R_TIMER     KB_ENCODER_TIM3
#define ENCODER_R_CHA_PORT  PORTB
#define ENCODER_R_CHA_PIN   PIN_4

#define ENCODER_R_CHB_PORT  PORTB
#define ENCODER_R_CHB_PIN   PIN_5
#define ENCODER_R_PIN_PULLUP NOPULL

/* Rane finders */
// ADC for range sensors
#define RECV_ADC            KB_ADC1
#define RECV_FR_PORT        GPIOC
#define RECV_FR_PIN         GPIO_PIN_0
#define RECV_R_PORT         GPIOC
#define RECV_R_PIN          GPIO_PIN_1
#define RECV_L_PORT         GPIOC
#define RECV_L_PIN          GPIO_PIN_2
#define RECV_FL_PORT        GPIOC
#define RECV_FL_PIN         GPIO_PIN_3

// Range sensor emitters
// right front : PC13
// sides : PA0
// left front : PA1
#define EMITTER_FR_PORT     GPIOC
#define EMITTER_FR_PIN      GPIO_PIN_13
#define EMITTER_L_PORT      GPIOA
#define EMITTER_L_PIN       GPIO_PIN_0
#define EMITTER_R_PORT      GPIOC
#define EMITTER_R_PIN       GPIO_PIN_14
#define EMITTER_FL_PORT     GPIOA
#define EMITTER_FL_PIN      GPIO_PIN_1


#endif /* BSP_WOLFIEMOUSE_KB_MODULE_CONFIG_H_ */

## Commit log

2015-12-13 Updated UART for virtual COM Port
2016-02-02 Added simulation and algorithm part - 80% completed.
    [maze.sdf]
2016-03-29 1. updated KiCad Schematics 2. updated the pinmap of the MCU
    [finder.sch, micromouse.kicad_pcb, micromouse.sch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]
2016-03-31 updated PCB design
    [finder.sch, micromouse.sch, motor.sch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]
2016-03-31 PCB updated
    [micromouse.dsn, micromouse.kicad_pcb, micromouse.sch]
2016-04-04 PCB board- needs to check the motor driver
    [finder.sch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]
2016-04-04 Finished the PCB
    [_saved_finder.sch, micromouse.kicad_pcb]
2016-04-04 PCB Completed
    [_saved_finder.sch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]
2016-04-04 Fixed for the PCB manufacturer requirements
    [micromouse-B.Cu.gbl, micromouse-B.Mask.gbs, micromouse-B.Paste.gbp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]
2016-04-05 Uploaded bill of materials
    [BOM.xlsx, micromouse.csv]
2016-04-05 Updated the algorithm part
    [maze.sdf]
2016-04-06 Changed the PCB design to meet the manufacturer's requirement
    [micromouse-B.Cu.gbl, micromouse-B.Mask.gbs, micromouse-B.Paste.gbp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]
2016-04-08 Made basic vl6180x and tca9545 drivers
2016-04-09 Fixed the 3.3V line problem of the right corner
    [micromouse.kicad_pcb]
2016-04-09 Printing and Saving simulation Good
2016-04-15 1. added the main project 2. changed the freq of the MCU, just for a while
    [micromouse.kicad_pcb]
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2016-04-16 encoder working - needs calibrate
2016-04-16 1.Rotary encoder works well 2.The measurements is added
2017-01-05 2017 Micromouse initial setup start
    [uSD_IMU_DIS.sch]
2017-01-14 provisioning for GNU ARM Eclipse
2017-01-24 updateCell() replaced with printMaze() in MouseController class. printMaze() overrides printMaze method in the MazeIO class
2017-01-24 printMaze in Maze class was made virtual
2017-01-24 Added the current class design
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2017-02-22 Added design goal for v2.0 and 3D models
    [Futura enhanced spacer.stl, skate.stl, solid wheel wide.stl]
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2017-03-21 Improved encoder update scheme
2017-03-21 Added simple pid control
2017-03-22 Added a new pcb board folder
    [Futura enhanced spacer.stl, finder.sch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]
2017-03-29 added BlackWolf hardware project - on progress!
    [BOM.xlsx, Sensor_Housing.STL, finder.sch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]
2017-03-30 BlackWolf PCB design completed
    [micromouse.kicad_pcb, micromouse.sch, uSD_IMU_DIS.sch]
2017-03-30 Changed Slikscreen
    [micromouse.kicad_pcb]
2017-03-30 PCB into production. Directory cleanup
    [micromouse-B.Cu.gbl, micromouse-B.Cu.gbr, micromouse-B.Mask.gbr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]
2017-04-02 Improved encoder update scheme
    Change name of peripherals.c
    Added simple pid control
2017-04-02 (no branch): Auto stash for cherrypick of "Improved encoder update scheme"
2017-04-04 added soldering notes for range sensors
    [finder.sch, micromouse.sch, motor.sch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]
2017-04-05 Divided project directory into boards
    [BOM.xlsx, Futura enhanced spacer.stl, Sensor_Housing.STL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]
2017-04-05 added basic ADC project to blinky
2017-04-05 added a simple sensor test in Nucleo-blinky
2017-04-06 Increase resolution of encoder by 8 times, basic pid speed control implemented
    [Futura enhanced spacer.stl, motor seat.STL, solid wheel wide.stl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]
2017-04-07 Speed-based PID PWM control updated
2017-04-07 Added range sensr-based rotational PID control
2017-04-07 A full roational PID solution
2017-04-20 Changed object model of motor and encoder
2018-03-07 PCB: Fixed wrong NMOS pinmap
    [micromouse.kicad_pcb]
2018-03-07 PCB: Fixed UART pins
    [finder.sch, micromouse.kicad_pcb, micromouse.sch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]
2018-03-07 PCB: Fixed floating PWM output problem
    [finder.sch, micromouse.kicad_pcb, micromouse.sch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]
2018-03-07 PCB: Added IR LED switch line
    [finder.sch, micromouse.kicad_pcb, micromouse.sch]
2018-03-08 PCB: Separated 5V source due to heat
    [micromouse.kicad_pcb]
2018-03-08 PCB: Added Via Stitching
    [micromouse.kicad_pcb]
2018-03-15 updated latest verison of STM32CubeMX
2018-03-15 CAM created
    [micromouse-B.Cu.gbl, micromouse-B.Mask.gbs, micromouse-B.Paste.gbp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]
2018-03-15 Added latest STM32F4 HAL from kb_lib
2018-03-15 Firmware: moved CMSIS, FreeRTOS, STM32HAL to lib folder
2018-03-15 Hardware: Updated STM32CubeMX project to remove fatfs
2018-03-16 Fimrware: First time successful flashing to Nucleo board using Makefile
2018-03-16 Blinkey: First successful flashing to WolfieMouse board using Makefile
2018-03-17 Blinkey: Added LED display test
2018-03-19 Blinky: Added Measuring rotary encoder
2018-03-20 ADC: Added R side pi for emitter. Added ADC test in blinky
2018-03-20 Encoder: changed to struct based
2018-03-20 Range: separated .c file for range sensor
2018-03-22 left/ right turn case algorithm fix
    [main.cc]
2018-03-22 left, right turn case during moving horizontal algorithm fix
    [main.cc]
2018-03-22 PID: set parameters for mouse. Working well
2018-03-22 PID: Adjusted for range sensor
2018-03-23 Forgot to switch the functions in main
2018-03-23 Mouse: Added Thread based motor control, not interrupt
2018-03-23 IMPORTANT: Best PID for forward moving, PWM frequency, baud rate changes
2018-03-23 PID: set a PID for rotational operation
2018-03-24 PID: added header file
2018-03-24 Measure: fixed PID and measurements
    [main.cc]
2018-03-24 Created competition mouse, fixed RealMouse
    [main.cc]
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2018-03-28 Hardware: Deleted v1.0 hardware
    [BOM.xlsx, Futura enhanced spacer.stl, Sensor_Housing.STL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]
2018-04-09 Moved RealMouse to board, add extension.json for VS Code
2018-04-09 MouseController: Fixed bug on moving, Introduced scanAndMove() to reduce redundant codes
    [main.cc]
2018-04-09 Fixed fakeIO files to FakeIO
    [main.cc]
2018-04-09 Fixed some compiler warnings
    [gpio.c, main.cc]
2019-03-01 Add kicad_ for KiCAD project
    [BOM.xlsx, Sensor_Housing.STL, finder.sch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]
2019-03-03 Main: Change FreeRTOS task name => thread to avoid name confilct with FSM tasks
    [main.cc]
2019-03-03 Main: Separated button handling functions
2019-03-03 Main: Added more helpful LED messages
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2019-03-04 Simulation_nucleo: Switch to terminal-based control instead of a button
2019-03-06 src: moved some headers in board to module (without modification)
2019-03-06 src: moved some headers in board to module (with modification)
2019-03-07 FSM: Fix issue with running next state's task instead of the current state.
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2019-03-09 Fix incorrect priority settings #73
    [main.cc]
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2019-08-08 Vagrant: Add appropriate kernel modules for USB drivers, update README
